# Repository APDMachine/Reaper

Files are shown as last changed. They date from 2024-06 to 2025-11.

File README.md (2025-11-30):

# [Reaper Toolhead](https://reapertoolhead.com)
### Toolhead Last Updated *03/07/2024*
### GitHub Last Updated *01/12/2025*
*Project Owner:*  [APD-Machines](https://github.com/APD-Machines)
*Maintained By:*  [KrauTech](https://github.com/krautech)

# Guides 

## > [Reaper Website](https://reapertoolhead.com)
## > [Reaper Configurator](https://reapertoolhead.com/?x=parts) <-- START HERE
## > [Installation Manual](https://reapertoolhead.com/?x=manual)



Join me on Discord (https://discord.gg/SHj5zEdzqZ)
> [!NOTE]
> This project is now completed and no longer being worked on by the designer however the community on discord is still strong and the project is community driven.
> USE AT YOUR OWN RISK

blownout

## Reaper uses a 3010 HE fan and dual 5015 part cooling fans.

## Supported hotends
- Phaetus Dragon Standard
- Phaetus Dragon HF
- Phaetus Dragon UHF
- Phaetus Rapido 1.0 HF/UHF
- Phaetus Rapido 2.0 HF/UHF
- Dropeffect NextG
- Dropeffect NextG UHF
- Revo Voron
- Slice Mosquito
- Slice Mosquito Magnum+
- BambuLab
- VZ Goliath
  
## Supported extruders
- Balrog
- Sherpa Mini
- Orbiter V2
- Hextrudort
- Hextrudort High
- LGX Lite V1 + V2
- LGX Lite Pro
- Hummingbird
- G2SA

***For all of these besides mine and the LGX’s you will need to sort out what
to do with the adjustment screw.***

## Supported probes
- TAP
- Beacon
- Cartographer
- Klicky PCB

assembly

# Original Inspiration
[Mantis Toolhead](https://github.com/mandryd/VoronUsers/tree/master/printer_mods/Long/Mantis_Dual_5015) was the initial inspiration behind Reaper and much thanks and credit to their initial work.
# Special Thanks
- [Long/Mandryd](https://github.com/mandryd/VoronUsers/tree/master/printer_mods/Long/Mantis_Dual_5015) for Mantis

Join me on Discord (https://discord.gg/SHj5zEdzqZ)

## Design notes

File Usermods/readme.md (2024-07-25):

Feel free to submit your own mods. Preferably in the following file tree
```
/Usermods
	/[Github Username]
		/Mod name
			/STL
			/CAD
			Readme.md
```

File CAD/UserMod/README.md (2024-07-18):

UserMods

*CAD SKILLS REQUIRED*
Use these step files to customize your Reaper for even more personilization.

For grill inserts build from the inside out keeping within the lipped ring. Try not to exceed 5.6mm total or travel could be affected.

Grill Logos, just cut out your own, real easy.

If you are using sensorless homing on a machine that does not use standard printed XY joints, be they carbon, laser, cnc. Use the BumStop files to make your own to match the thickness and geometry of your setup.

The SaladFork BumStops could possibly be used to make mods for Micron printers.

We do NOT recommend using Reaper on anything smaller than a 160 build for any reason. But if you want to be ridiculous just to be ridiculous then we wont stop you!

As always if your usermods work, please post them on the discord so others may have access. We will come up with links to them later.

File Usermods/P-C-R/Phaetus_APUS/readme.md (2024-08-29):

# Mount for Phateus APUS
* Modded orbiter 2.0 mount. Mounting holes still in place
* No Problem with tension screw as the Apus tension screw is in the front
* For Toolboard moutn use this: https://www.printables.com/de/model/332760-eva-3-ebb36-and-ebb42-mounts-for-phaetus-apus-extr

## Hardware needed
* 6x M3 Heat Inserts (VORON style)
* 4x M3x12 Socket Head
* (optional) 2x M3x10 Button Head

APUS_IMAGE

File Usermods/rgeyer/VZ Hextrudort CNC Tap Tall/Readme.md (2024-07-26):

This modifies the TAP extruder mount for the VZ Hextrudort (low) extruder. `STL/Extruder Mounts/TAP/HextrudortLOW CNC TAP.stl`

All it really does, is moves the extruder another 4mm away from the hotend, allowing the tension screw to *just* clear the right 5015 fan.

I've been testing it for about 48hr worth of prints, and it's working as expected!

Just the extruder mount and extruder
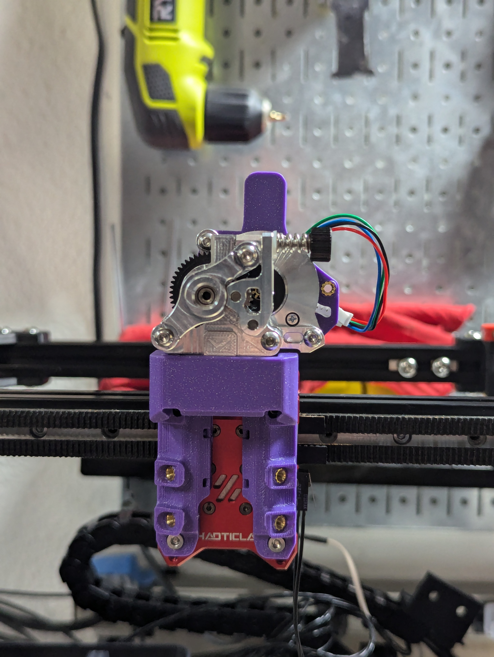
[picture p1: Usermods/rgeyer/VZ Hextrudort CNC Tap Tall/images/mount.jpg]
extruder mount


Clearance
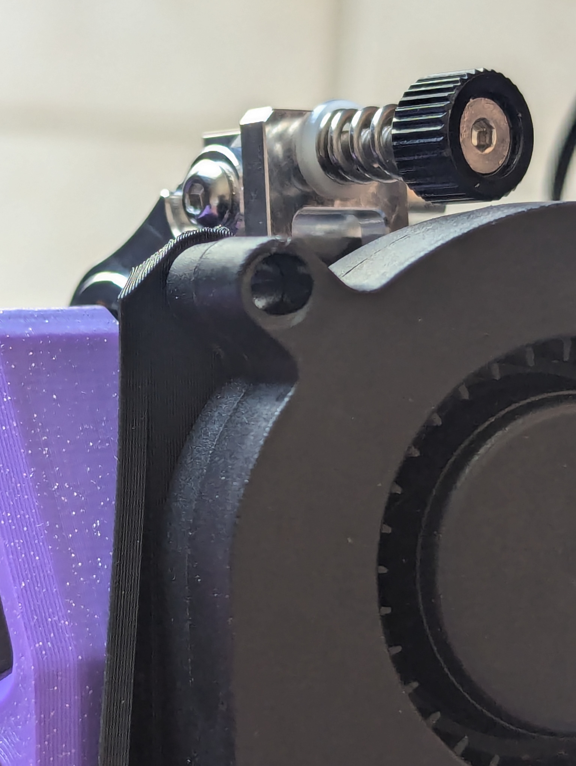
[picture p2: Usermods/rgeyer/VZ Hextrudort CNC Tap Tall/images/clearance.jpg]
clearance


This is what it looks like all together.
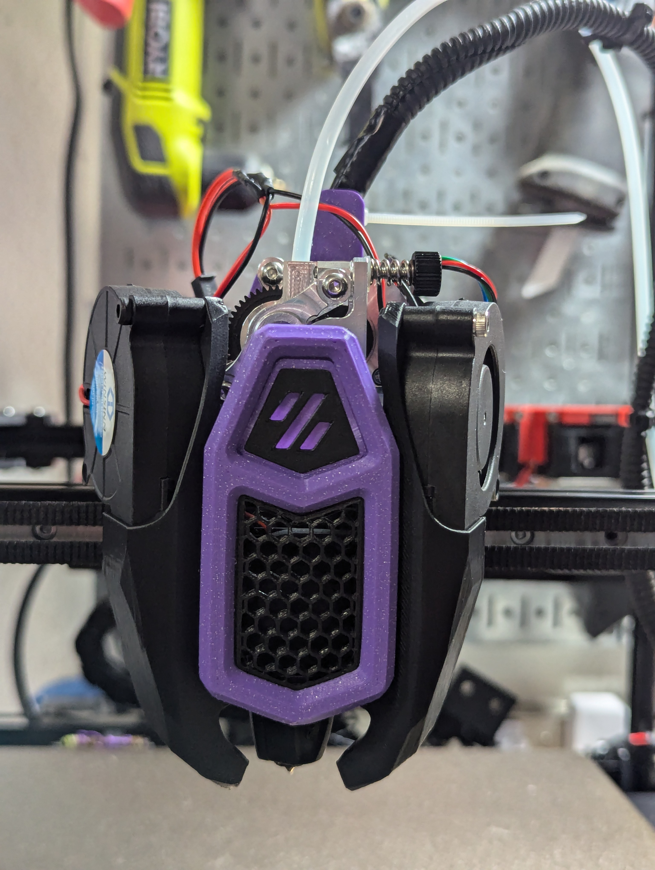
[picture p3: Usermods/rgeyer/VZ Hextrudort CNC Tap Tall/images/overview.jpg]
overview


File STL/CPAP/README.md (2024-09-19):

# [Reaper Toolhead](https://apdm.tech)
### Last Updated *03/07/2024*
*Project Owner:* [APD-Machines](https://github.com/APD-Machines)

# Guides 

## > [APDM Website](https://apdm.tech)

Join me on Discord (https://discord.gg/SHj5zEdzqZ)
> [!NOTE]
> This project is under-going heavy testing and there are changes happening all the time. 
> USE AT YOUR OWN RISK

This is a first iteration on CPAP integration for Reaper. 
THESE PARTS ARE STILL UNDERGOING DEVELOPMENT AND CHANGES.

*Use Classic Wall Generator in your slicer, Arachne has issues with thin walls and/or gap fill and will cause surface quality issues.*

***You will need to add support to the bottom sections of the interface as well as under the mount ear. There is an image on the Discord in #reapers-blow-cpap showing where. These are the only places supports are needed until we sort out built in supports in the model.***

Join me on Discord (https://discord.gg/SHj5zEdzqZ)

# Special Thanks
- [Printstructor] For taking care of the built in suppors for the CPAP adapter.

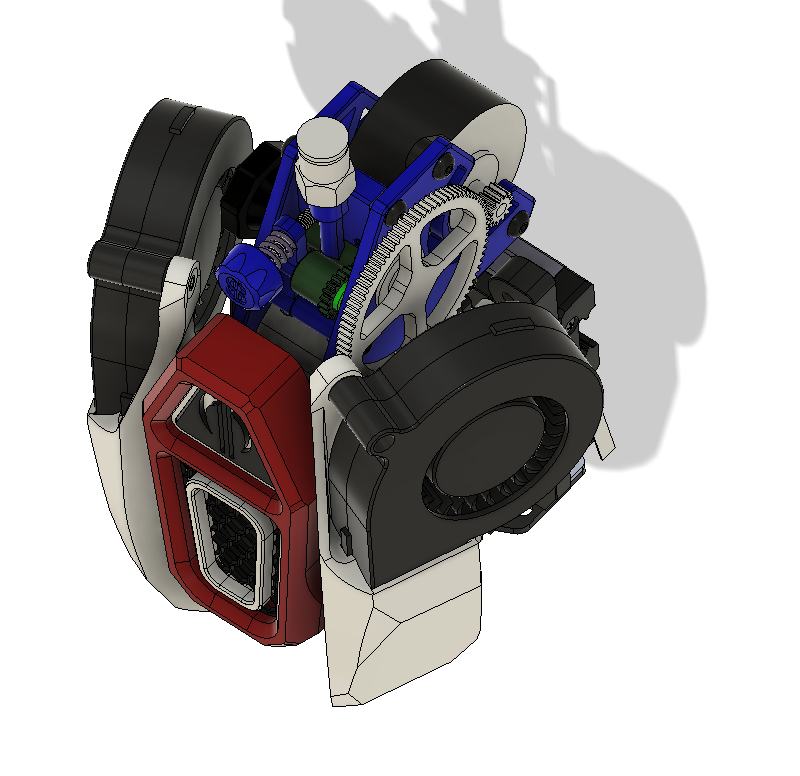
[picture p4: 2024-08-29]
Usermods/P-C-R/Phaetus_APUS/APUS_IMAGE.png

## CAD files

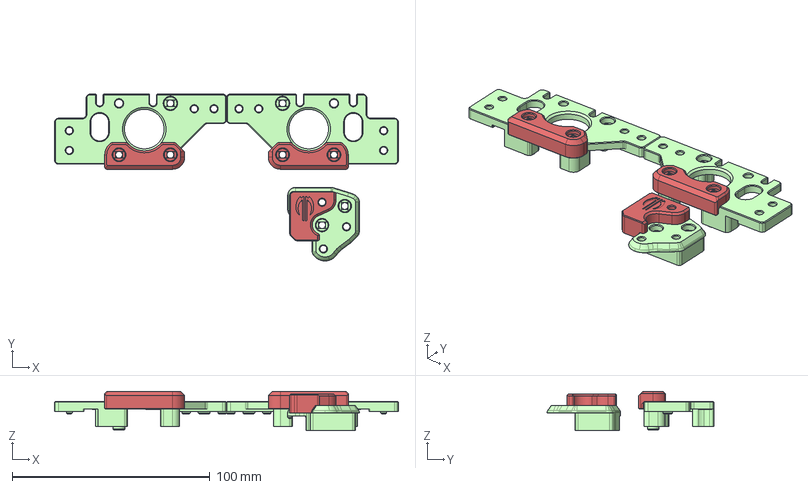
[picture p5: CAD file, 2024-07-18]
CAD/UserMod/Gantry/Salad Fork BumStops.step
174.0 x 84.4 x 19.8 mm
xy_joint_upper_right_x1.step
A_Drive_Frame_Upper_x1.step

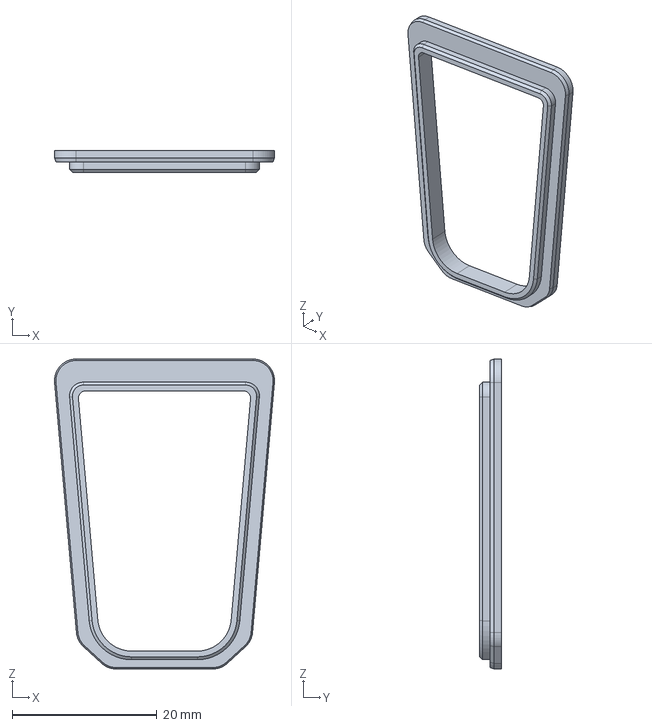
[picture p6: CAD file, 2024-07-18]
CAD/UserMod/Grills/Grill T2 Insert Blank.step
30.4 x 3.00 x 42.8 mm

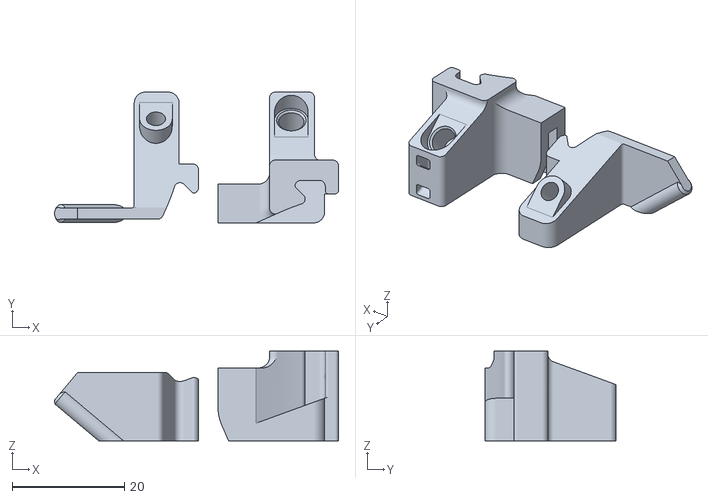
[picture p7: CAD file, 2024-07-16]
STL/1st PRINT Fitment Benchmark.stl
50.5 x 23.3 x 16.0

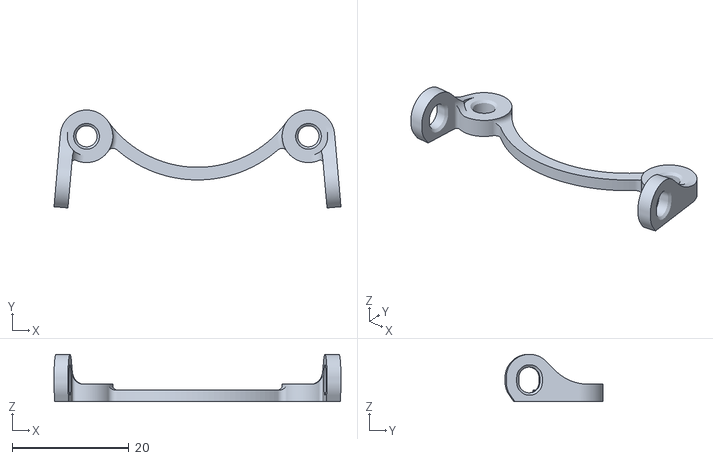
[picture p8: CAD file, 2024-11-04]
STL/Board Mounts/MGN12H Side Mount.stl
49.1 x 16.8 x 8.11

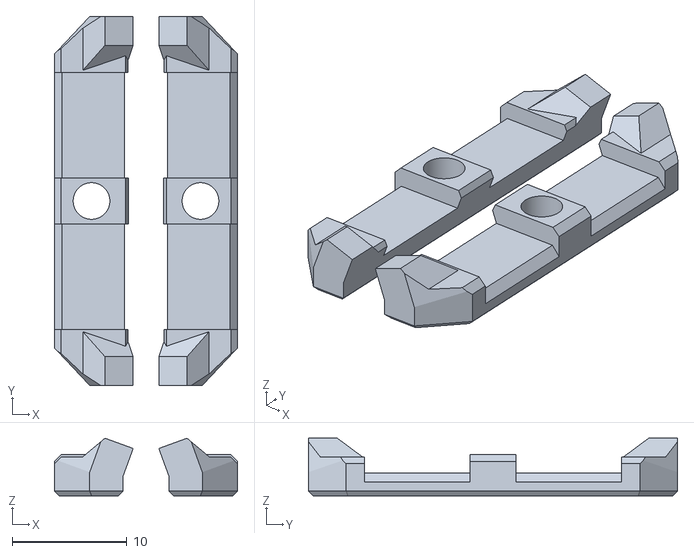
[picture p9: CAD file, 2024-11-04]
STL/Carriages/Belt Clamp 9mm.stl
16.0 x 32.2 x 5.02

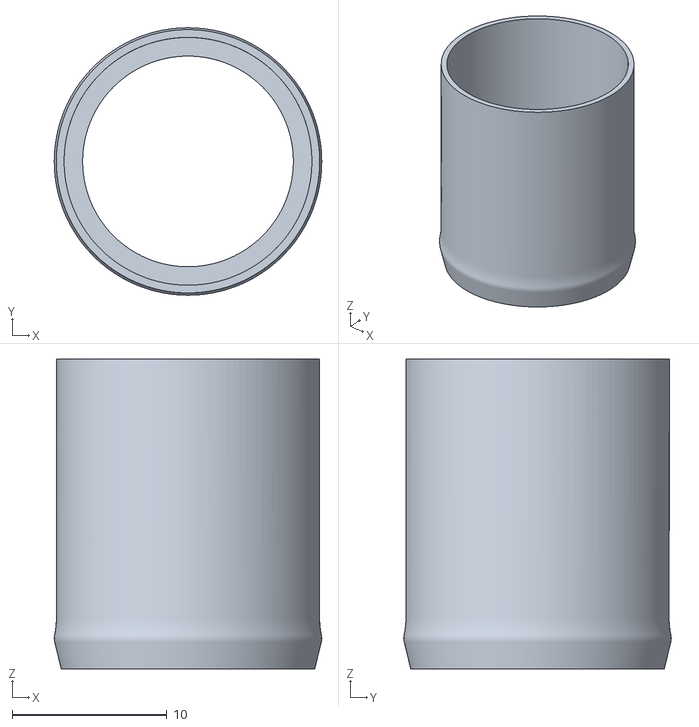
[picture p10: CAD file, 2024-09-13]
STL/CPAP/17mm CPAP Adapter.stl
17.3 x 17.3 x 20.0

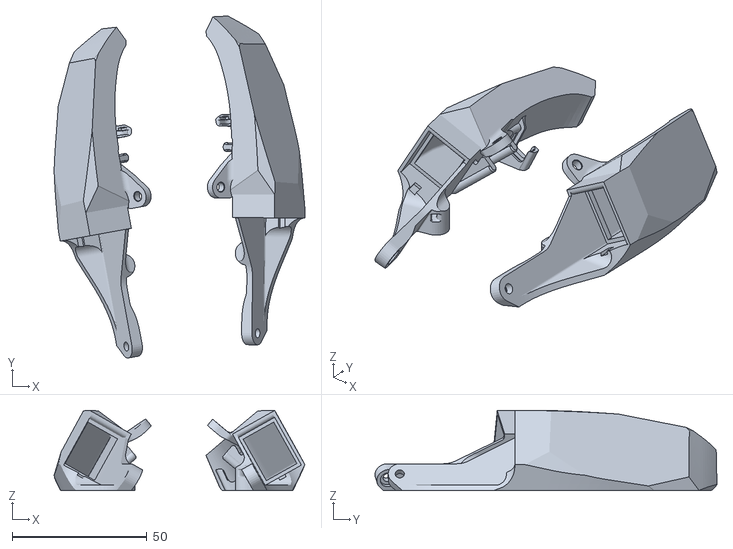
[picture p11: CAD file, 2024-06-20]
STL/Ducts/Overkill/Overkill LED.stl
92.9 x 126.7 x 29.6

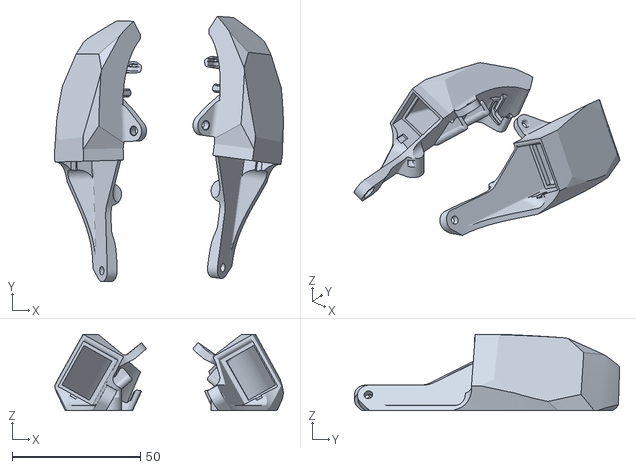
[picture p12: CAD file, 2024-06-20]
STL/Ducts/Standard/Standard LED.stl
89.2 x 103.3 x 29.6

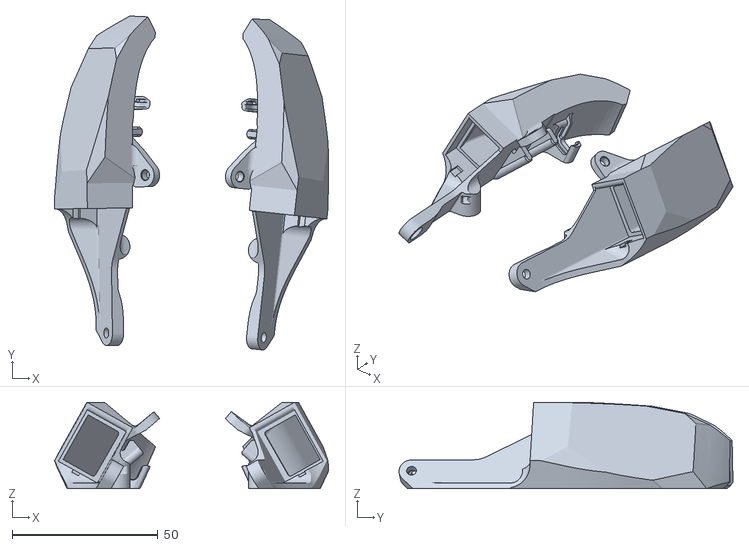
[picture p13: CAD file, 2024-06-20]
STL/Ducts/UHF/UHF LED.stl
94.0 x 114.6 x 29.6

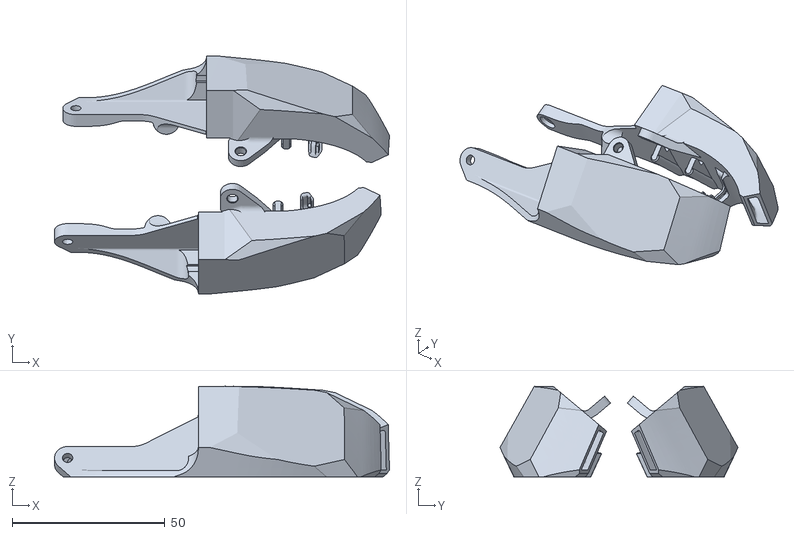
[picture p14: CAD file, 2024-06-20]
STL/Ducts/Volcano/Volcano LED.stl
109.7 x 77.9 x 29.6

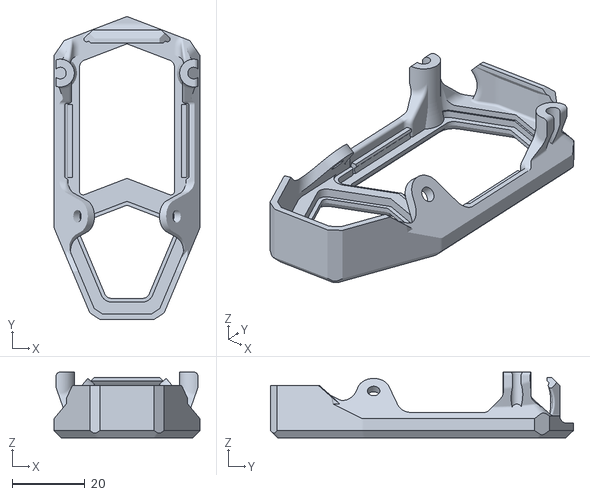
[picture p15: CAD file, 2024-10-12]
STL/Grill/Type 1/Grill T1 Shell - NoLed.stl
40.0 x 83.0 x 18.0

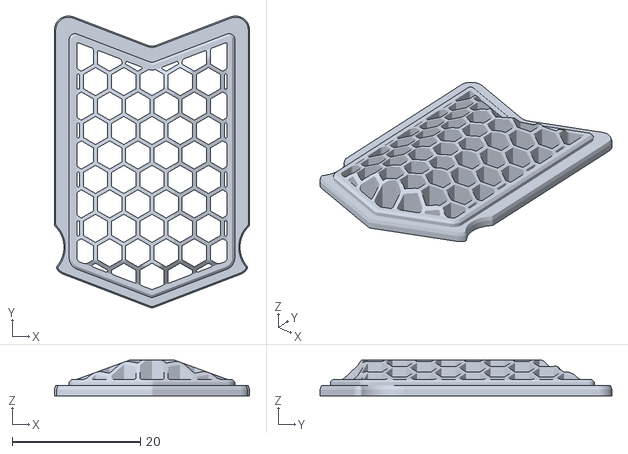
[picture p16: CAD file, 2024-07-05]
STL/Grill/Type 1/Inserts/Grill T1 Insert 3dhoneycomb.stl
30.4 x 45.5 x 5.60

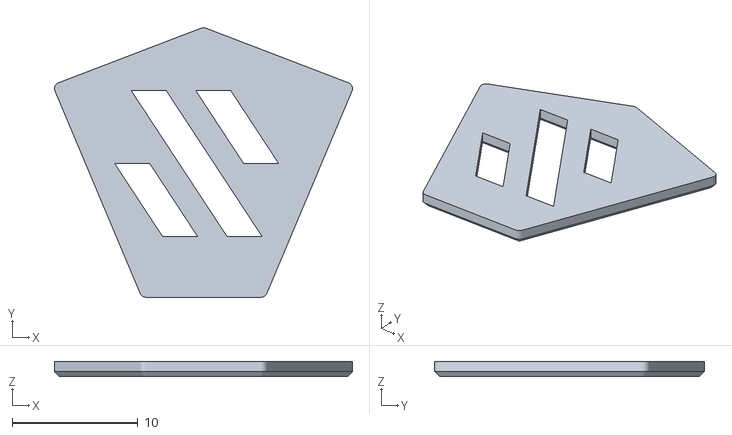
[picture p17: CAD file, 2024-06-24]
STL/Grill/Type 1/Logo Plate/Grill T1 Logo Plate Voron.stl
23.7 x 21.4 x 1.20

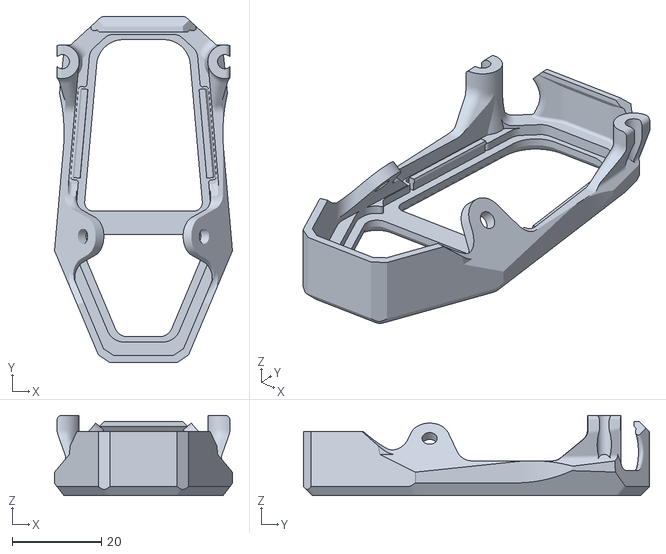
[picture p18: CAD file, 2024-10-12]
STL/Grill/Type 2/Grill T2 Shell - NoLed.stl
40.0 x 77.8 x 18.0

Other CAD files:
STL/Grill/Type 2/Inserts/Grill T2 Insert 2PC A.stl
STL/Grill/Type 2/Logo Plate/Grill T2 Logo Plate APD.stl
STL/Misc/SaladFork BumStops.stl
STL/Probes/BeaconCartographer/BeaconCartographer Standard.stl
CAD/UserMod/Grills/Grill T1 Insert Blank.step
CAD/UserMod/Grills/Grill T1 Logo Blank.step
CAD/UserMod/Grills/Grill T2 Logo Blank.step
STL/Board Mounts/Ebb36 Balrog.stl
STL/Board Mounts/Ebb36 Hextrudort.stl
STL/Board Mounts/Ebb36 LGX Lite Pro.stl
STL/Board Mounts/Ebb36 Sherpa.stl
STL/Board Mounts/Ebb36 WWG2.stl
STL/Board Mounts/MGN12H Beefy Side Mount.stl
STL/Board Mounts/MGN9H Side Mount.stl
STL/CPAP/19mm CPAP Adapter.stl
STL/CPAP/22mm CPAP Adapter.stl
STL/Carriages/Belt Clamp 6mm.stl
STL/Carriages/MGN12H 6mm.stl
STL/Carriages/MGN12H 9mm.stl
STL/Ducts/Overkill/Overkill noLED.stl
STL/Ducts/Standard/Standard noLED.stl
STL/Ducts/UHF/UHF noLED.stl
STL/Ducts/Volcano/Volcano noLED.stl
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

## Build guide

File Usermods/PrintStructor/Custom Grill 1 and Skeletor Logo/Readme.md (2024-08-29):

# Grill 1 - Cheese Grater Insert - Skeletor Logo - Bugfix for Lower Grill Shell Clamp 

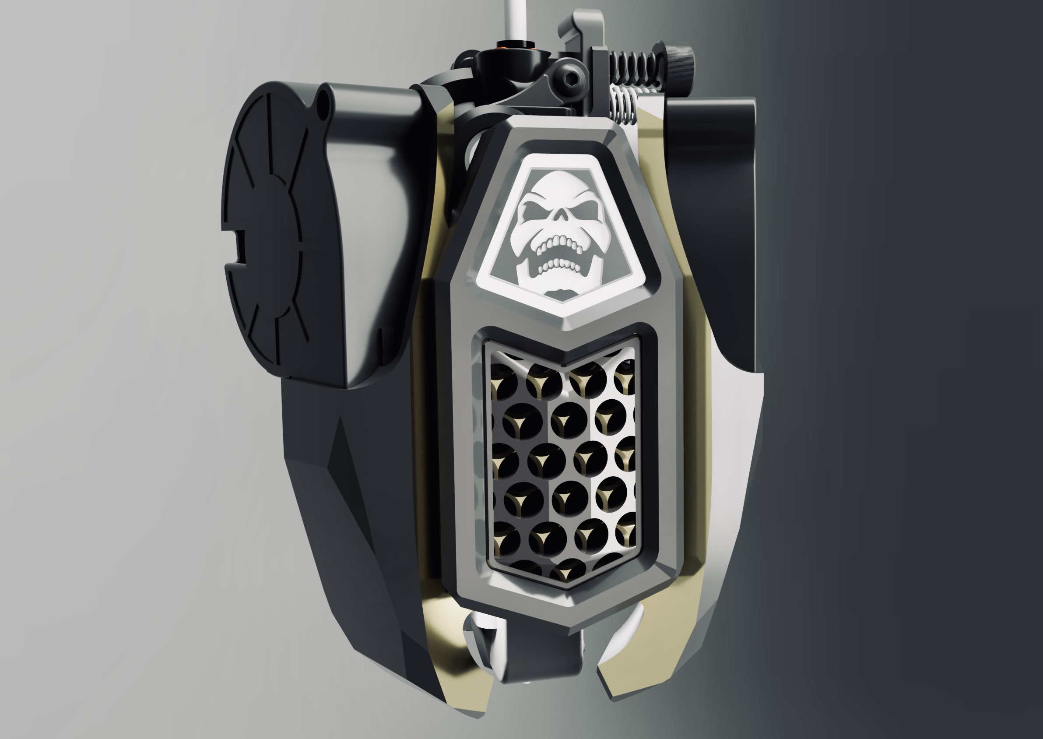
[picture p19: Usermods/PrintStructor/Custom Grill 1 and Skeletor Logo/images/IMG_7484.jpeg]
Image of reaper toolhead


Here you can find a custom grill insert in cheese grater design. I have also released the stealth skirts for the VORON 2.4 and Trident to match. 

I've also added the good old He-Man Skeletor logo and repositioned and lengthened the lower mounting clamp of the grill shell so that it now rests against the underside of the hotend mount.
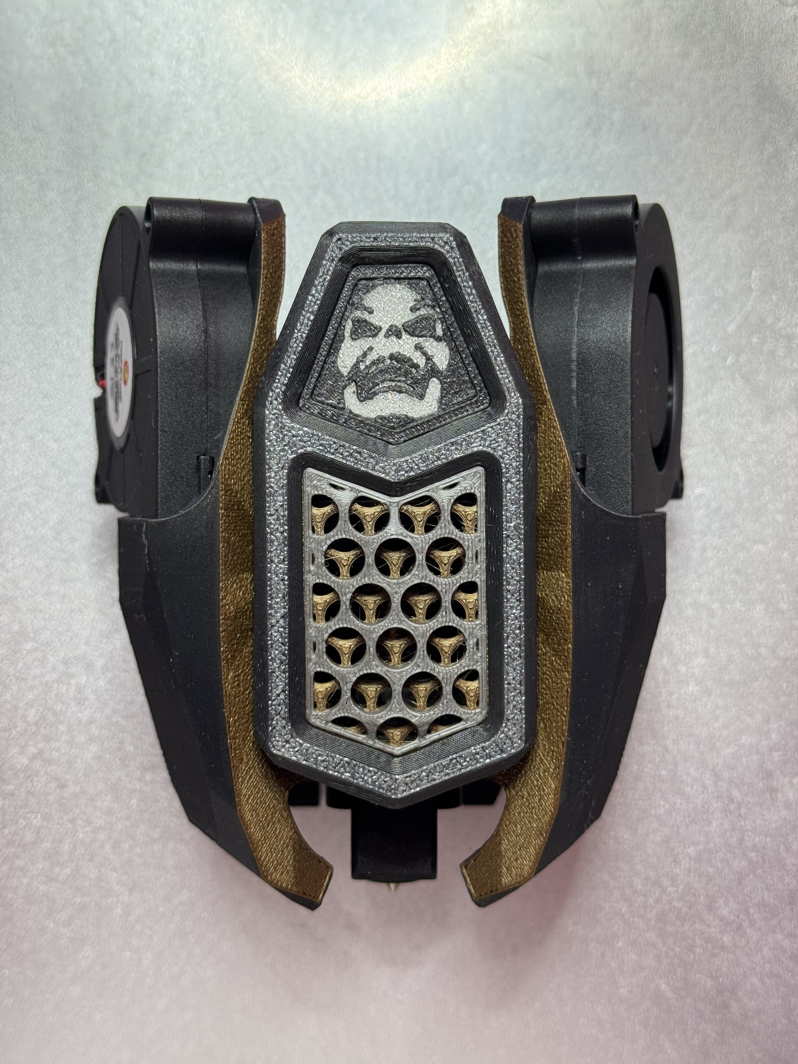
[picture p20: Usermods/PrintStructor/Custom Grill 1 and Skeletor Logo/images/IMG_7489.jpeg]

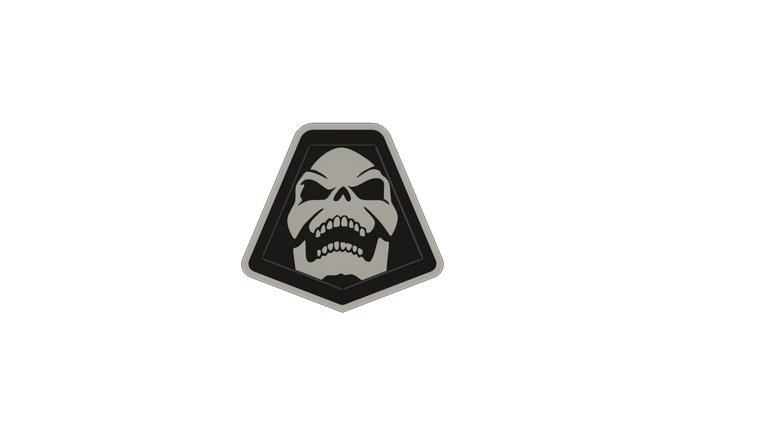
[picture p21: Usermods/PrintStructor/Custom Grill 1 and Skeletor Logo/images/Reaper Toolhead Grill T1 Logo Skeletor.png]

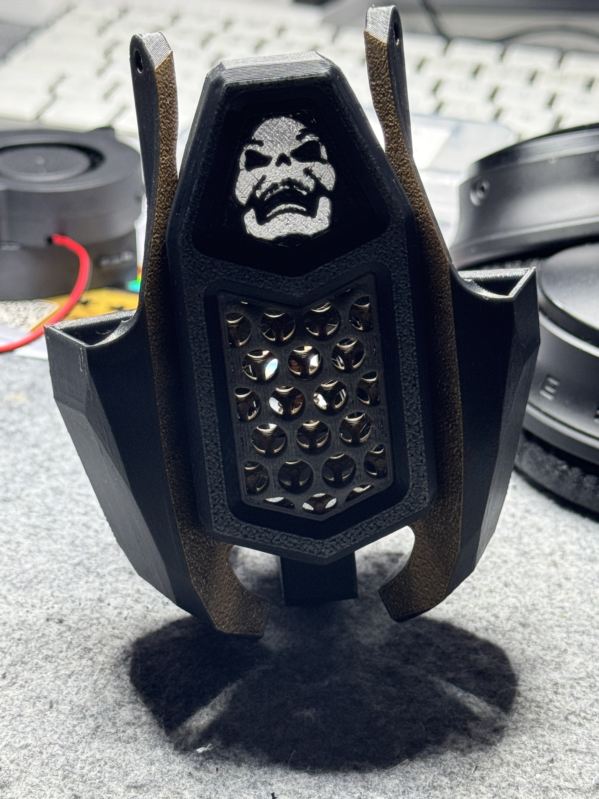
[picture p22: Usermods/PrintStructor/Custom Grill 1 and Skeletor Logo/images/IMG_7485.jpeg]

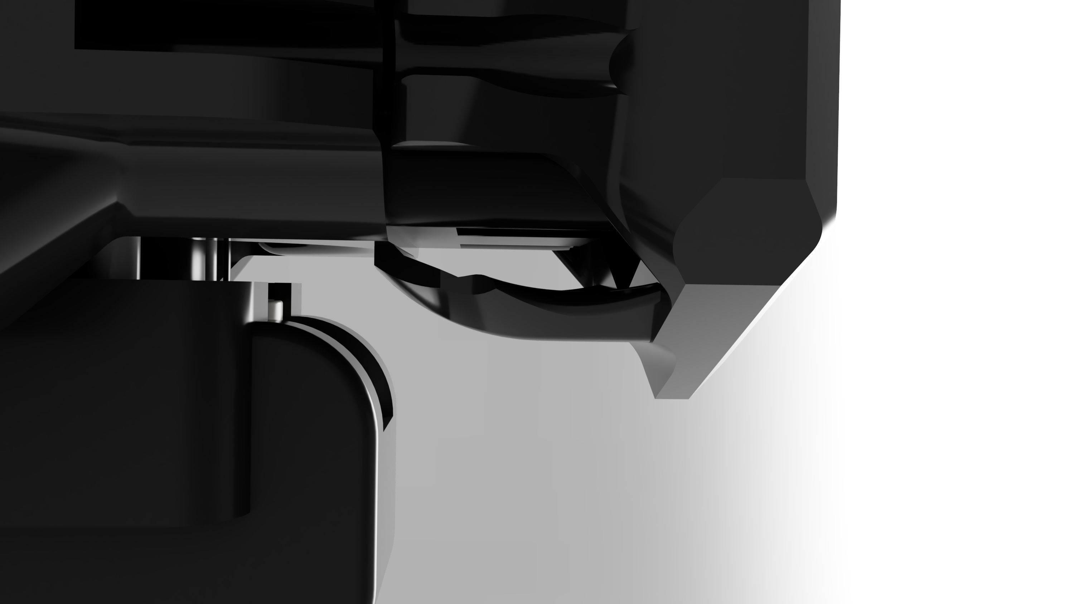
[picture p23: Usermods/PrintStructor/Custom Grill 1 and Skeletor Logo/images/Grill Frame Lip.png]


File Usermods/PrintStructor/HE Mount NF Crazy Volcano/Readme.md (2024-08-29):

# Hotend Mount for Mellow NF Crazy Volcano (should also work for Mosquito Magnum) 

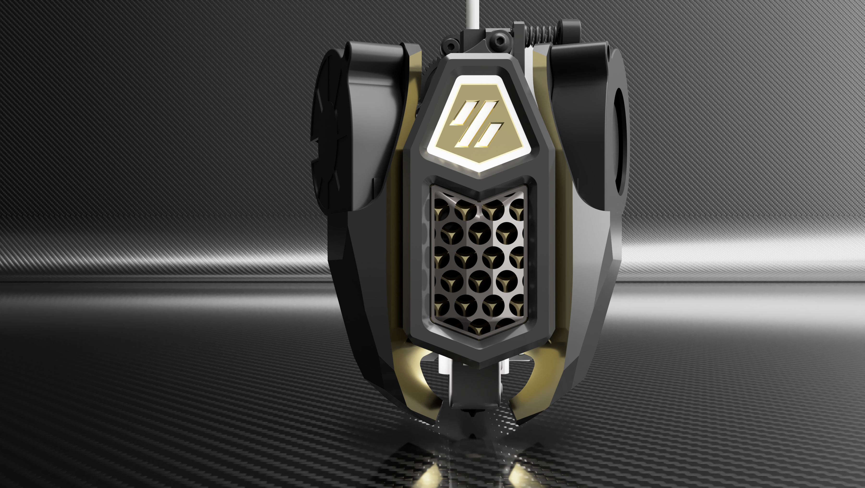
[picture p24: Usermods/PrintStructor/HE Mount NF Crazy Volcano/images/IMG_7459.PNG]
Image of reaper toolhead


I designed the opening for the fan on the front so that there is as much open space as possible. The air is then channelled cleanly to the rear directly to the heatbreak and flows around it optimally. I also created 2 optional holes at the top for a complete screw connection of the fan. 
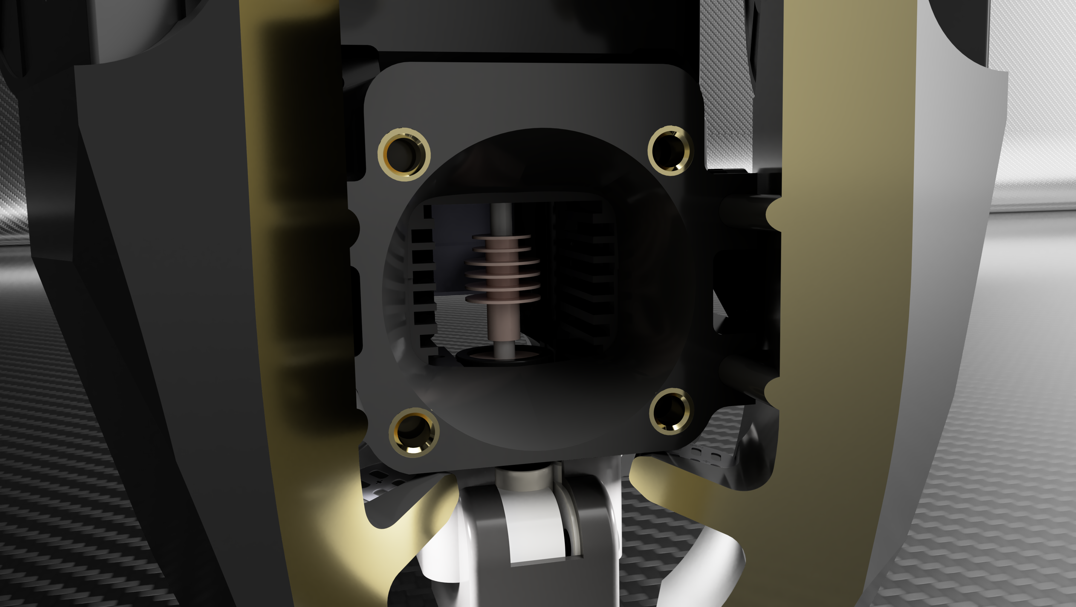
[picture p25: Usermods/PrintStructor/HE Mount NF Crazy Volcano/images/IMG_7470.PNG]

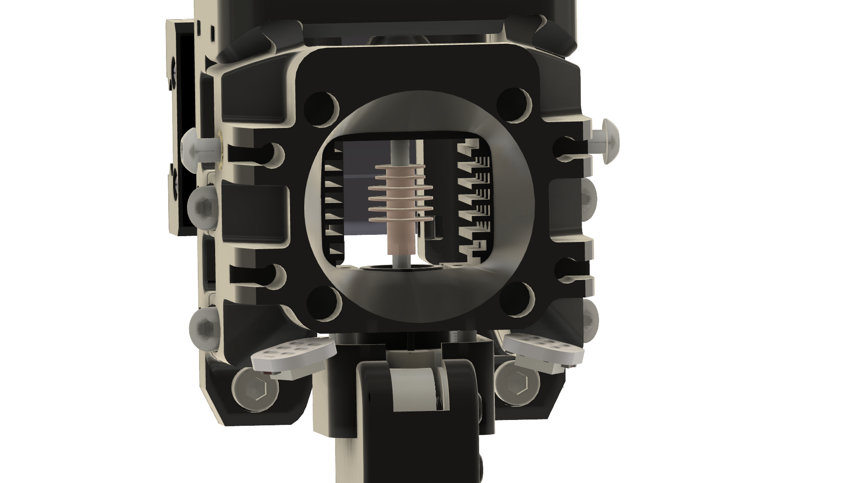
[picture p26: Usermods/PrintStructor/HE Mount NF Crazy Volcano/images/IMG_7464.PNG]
Image of hotend nount


The upper attachment point for the two hotend screws was given small fixing points for mounting and the screw guides were adapted to the screw length of the hotend. Overall, the hotend has been moved upwards by several mm so that it is now at the same height as the Rapido. The ducts should now be optimally aligned with the nozzle. I have removed some material in the lower area so that it is easier to get to the rear with the cable from the thermistor or heater.  
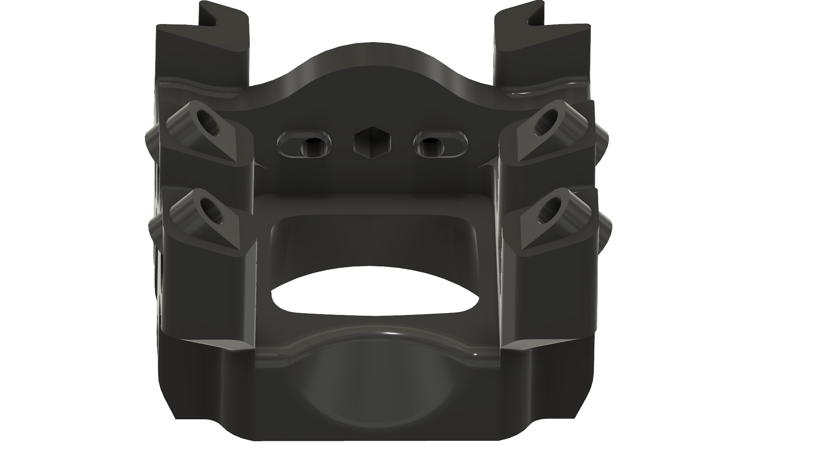
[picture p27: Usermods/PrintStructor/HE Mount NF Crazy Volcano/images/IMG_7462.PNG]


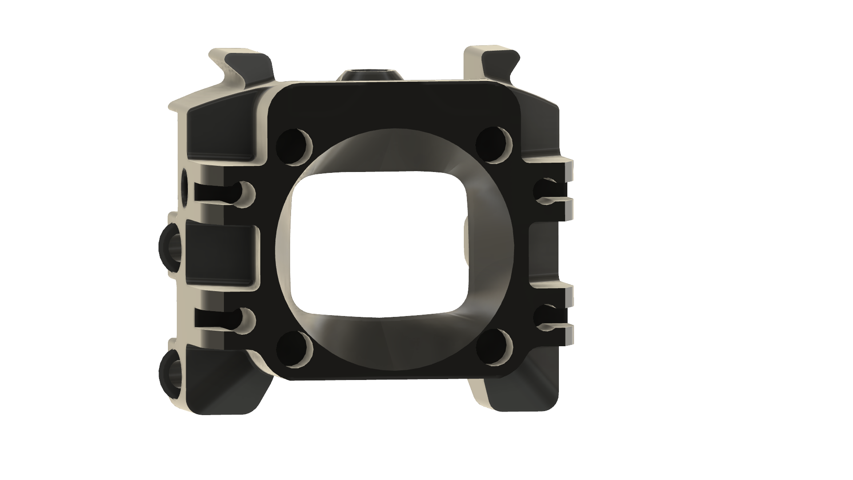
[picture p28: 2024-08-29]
Usermods/PrintStructor/HE Mount NF Crazy Volcano/images/IMG_7463.PNG

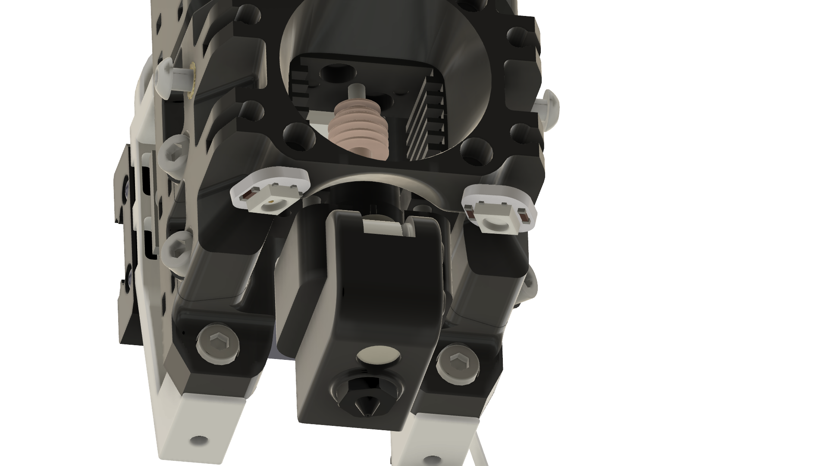
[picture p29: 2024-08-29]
Usermods/PrintStructor/HE Mount NF Crazy Volcano/images/IMG_7466.PNG

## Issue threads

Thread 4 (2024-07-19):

Reaper Configurator directs "Printed TAP" into Github's "CNC TAP" folder for extruders

PeterXQC, 2024-07-19:
**Describe the bug**
Reaper Configurator directs "Printed TAP" into Github's "CNC TAP" folder for extruders.

**To Reproduce**
Steps to reproduce the behavior:
1. Go to Reaper Configurator
2. Configure as:
    [Printed Tap](https://apdm.tech/?x=parts&step=1)
    [Rapido V2 UHF](https://apdm.tech/?x=parts&step=2&carriage=printed%20tap)
    [Orbiter V2.0](https://apdm.tech/?x=parts&step=3&carriage=printed%20tap&hotend=Rapido%20V2%20UHF)
    [MGN12H](https://apdm.tech/?x=parts&step=4&carriage=printed%20tap&hotend=Rapido%20V2%20UHF&extruder=Orbiter%20V2.0)
    [6MM](https://apdm.tech/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)
    [Tap](https://apdm.tech/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)
    [Grill Type 2](https://apdm.tech/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)
    [1PC](https://apdm.tech/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)
    [Voron](https://apdm.tech/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)
    [Yes](https://apdm.tech/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)

**Expected behavior**
The list of STLs to download should direct to correct locations of this Repo

**Filename**
STL/Extruder Mounts/TAP/OrbiterV2.0 Printed TAP.stl Does Not Exist

krautech, 2024-07-19:
Interesting, I'll take a look at this now.

Thank you for reporting. Ill keep you updated!

krautech, 2024-07-20:
This should now be corrected. Please re-open if you continue to experience issues.

Closed 2024-07-20.

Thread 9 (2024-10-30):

Possible to squeeze a filament sensor in somewhere ?

Glenno-H, 2024-10-30:
While things look very tight, I was hoping there might be room to squeeze in a filament sensor somehow ?  It would be great for use with endless spool / ERCF systems...

flyespresso, 2024-10-30:
Hop on our discord, it's been done, that's entirely dependent on what extruder you're using. It's not part of the baseline as we have so many configurations supported–but there is sensor mods already with a search on discord! (Hartk has one for example)

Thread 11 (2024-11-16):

Add spider V3 pro (or unified model Step for DIY)

Zirus-VAG, 2024-11-16:
**Is your feature request related to a problem? Please describe.**
Use of not yet supported hotend

**Describe the solution you'd like**
Hotend mound: May I ask to get a Mount for Spider V3 pro

**Describe alternatives you've considered**
alternative: a step file with centerline and nozzle end where I can substract a block of my selected hotend) - Remix of covers are perfectly done! -Thanks!)

**Discord Username**
Zirus-VAG

**Additional context**
Thanks for this great looking and performing toolhead!

krautech, 2024-11-16:
Happen to have a CAD available of your hotend? I can look into this for you while Alex is away

editwentyone, 2025-01-01:
https://grabcad.com/library/creality-spider-pro-hotend-1

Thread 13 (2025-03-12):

RGB LED support

oernster, 2025-03-12:
Hi.  Great toolhead.  Love it.

I have it installed and it's working beautifully.

However, I was wondering about the possibility of RGB LEDs.
Can I use the default wiring harness that you would normally use with e.g. a Stealthburner (e.g. Rainbow BARF leds) or do you need to rewire/solder the harness like you would have to for a Dragon/Rapid Burner?

Thanks.
Oliver

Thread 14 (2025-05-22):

Request for CPAP Duct for Goliath Hotend or STEP Files for Customization

spl420, 2025-05-22:
Hi there,

First of all, thank you for your amazing work on the Reaper Toolhead – it’s truly impressive!

I’m currently using the Goliath hotend and would love to have a compatible CPAP duct. Would it be possible to get a version of the duct that fits the Goliath? Alternatively, if you could share the STEP files for the UHF duct, I’d be happy to modify it myself to fit the Goliath setup.

That would be incredibly helpful – thanks a lot in advance!

Best regards,
Jakob

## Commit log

2024-06-20 Added Entire STL Components
    [Chube Naked.stl, Chube noGrill.stl, G2SE - TAP.stl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]
2024-06-20 Added Carriage Information to part selection guide
2024-06-20 Fixed File names and added carriages
    [Reaper Overkill Beacon Cartographer.stl, Reaper Standard Beacon Cartographer.stl, Reaper Standard Beacon Cartographer.stl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]
2024-06-21 corrected orientation of logo plates
    [Grill T1 Logo Plate Blank.stl, Grill T1 Logo Plate Voron.stl]
2024-06-24 Update to Grills
    New geometry to prevent breakage.
    Shells are updated.
    Honeycomb inserts are updated.
    Grill T1 VSlot is the same as well as logo plate holders.
    New Logo Plates added.
    [Grill T1 Insert 3dhoneycomb.stl, Grill T1 Insert DIY.stl, Grill T1 Logo Plate APD.stl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]
2024-06-24 Create Grill T1 Shell - No Support.stl
    [Grill T1 Shell - No Support.stl]
2024-06-24 File Renames
    [Reaper Overkill Beacon Cartographer.stl, Reaper Standard Beacon Cartographer.stl, Reaper UHF Beacon Cartographer.stl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]
2024-06-26 Grill 1 & 2 Updates
    - Changed geometry for added support to minimize breakage
    [Grill T2 Shell - No Support.stl]
2024-06-30 Occlusion Removal
    Removed occlusions that have caused quality issues during printing.
    Also added 2 mounts that were not previously uploaded.
2024-07-01 Added Extruder Warning - Tensioner
2024-07-03 Added Reaper CAD & XY Joint Limit Switch
    STEP File is in a ZIP due to being over 100MB (111MB)
    [XY Joint Limit Switch Pod.stl]
2024-07-03 Removed DUCTS Naked and No Grill and Renamed Works to LED
    [Chube Naked.stl, Chube noGrill.stl, Overkill LED.stl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]
2024-07-03 Fixed Naming Schema
    [Reaper Overkill Beacon Cartographer.stl, Reaper Standard Beacon Cartographer.stl, Reaper UHF Beacon Cartographer.stl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]
2024-07-03 Removed UHF naming from Rapido
    Rapido UHF and HF use same hotend mount
2024-07-04 added grill type 1 barf led test shell
2024-07-05 Whoopsies on belt spacing
    Geometry corrected to proper belt spacing for all 6mm MGN12H Reaper Carriages
    [Reaper Overkill Beacon Cartographer.stl, Reaper Standard Beacon Cartographer.stl, Reaper Standard Klicky.stl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]
2024-07-05 Belt Spacing fix
    Fixed the belt spacing whoopsie.
2024-07-05 Small Geometry changes to assist in printing and assembly
    Duct changes include 7mm countersink for those using screw/nut vs HSI in fan. Notch included for fitting nozzle LEDs.
    Updated geometry for Honeycomb pattern grill inserts to work easier with varying slicers.
    [Grill T1 Insert 3dhoneycomb.stl, Grill T2 Insert 1PC.stl, Grill T2 Insert 2PC A.stl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]
2024-07-12 More better carriages.
    Changed location of x endstop switch to trigger on Voron XY joint.
    Added provisions for wiring for probes.
2024-07-13 Removed Obsolete Files
    [XY Joint Limit Switch Pod.stl]
2024-07-13 Revert "Removed Obsolete Files"
    This reverts commit a7fadd4570f7b0bb0c93c5b24b1bd90a3d853363.
    [XY Joint Limit Switch Pod.stl]
2024-07-13 Remove Obsolete Files
    [XY Joint Limit Switch Pod.stl]
2024-07-13 Endstop fix and BumStops
    Reaper Carriages with fixed positioning for mounted endstop switch.
    Separated BumStops for Sensorless homing.
    [12H BumStop.stl, 9H BumStop.stl, Ants BumStops.stl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]
2024-07-15 Updates to Manual and Extruder mounts
    Manual has been updated to match new Reaper carriages for X endstop switch and quick probe wiring suggestion.
    New Extruder mounts:
    - Updated Sherpa mounts to include 3rd screw.
    -Printed TAP mounts for any TAP and/or CNC TAP with non-flush mounted screws.
2024-07-15 Updated 9H Reaper Carriages
    Updated with new endstop switch mount.
2024-07-16 Fitment Benchmark
    Print first for less future issues.
    [PRINT FIRST Fitment Benchmark.stl]
2024-07-16 PRINT THIS FIRST
    Fitment benchmark to make sure of fitment on interlocking features.
    [1st PRINT Fitment Benchmark.stl]
2024-07-18 Step Files for user mods
    Use these to customize your own or adapt parts for your particular setup.
    [Grill T1 Insert Blank.step, Grill T1 Logo Blank.step, Grill T2 Insert Blank.step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]
2024-07-18 Updated G2SA Mounts
    Now have 3rd bolt support.
2024-07-26 It'd be good to actually include the files
    [HextrudortLOW CNC TAP.3mf, HextrudortLOW CNC TAP.step, HextrudortLOW CNC TAP.stl]
2024-07-27 Dum Dum Fix
    They are actually now MGN12H 9mm Belt Carriages, whoopsies.
2024-08-01 Update README.md
    Fan descriptions added.
2024-08-07 Create PrintStructor
2024-08-07 Created user folder and uploaded first files
    [HE MOUNT NF CRAZY Volcano.step, HE MOUNT NF CRAZY Volcano.stl]
2024-08-07 Created folder Custom Grill and uploaded files
    [Grill T1 Insert Cheese Grater.step, Grill T1 Insert Cheese Grater.stl, Grill T1 Logo Plate Holder.stl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]
2024-08-17 Reaper - Carriages Fixed
    Deleted Weird Carriages
    [Reaper Standard Klicky.stl, Reaper UFH Klicky.stl, Reaper UHF Klicky.stl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]
2024-08-29 VINDR Ducts
    Due to increasing popularity and support from West3d we now have VINDR specific ducts that no longer require modification to get them to fit.
2024-09-13 CAD and STLs
    Fuller CAD files added for User Mods
    Revised BumStops
    Revised VINDR Ducts
    CPAP added
    [12H BumStop.stl, 9H BumStop.stl, Ants BumStops.stl]
2024-09-13 CPAP Hose Adapters
    Hose adapters for 17mm, 19mm, and 22mm ID hoses.
    [17mm CPAP Adapter.stl, 19mm CPAP Adapter.stl, 22mm CPAP Adapter.stl]
2024-09-13 Geometry change
    Fix Left Ducts
2024-09-14 Eliminate Thin Wall
    Updated geometry to eliminate thin wall print quality issues.
2024-09-18 LED Holder Fix
    Updated the LED holder for less breakage and easier installation.
    Also removed the wiring notches on the keys on the NoLED versions.
2024-09-18 CPAP Update
    CPAP updated to eliminate hidden thin walls, better LED mounts, built in supports on CPAP Adapter.
2024-10-12 Updated LED support
    [Grill T1 Shell - NoLed.stl, Grill T2 Shell - No Support.stl, Grill T2 Shell - NoLed.stl]
2024-11-04 Added Carriage v1.whatever and new extruder mounts etc
    [12H BumStop - Old.stl, 12H BumStop.stl, 9H BumStop - Old.stl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]
